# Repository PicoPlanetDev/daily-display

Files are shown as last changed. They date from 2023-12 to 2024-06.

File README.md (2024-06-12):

# daily-display

This README is a work in progress.

## Overview

Designed to be displayed on a wall-mounted screen, Daily Display combines a calendar of tasks 
for each day with a pill dispenser and reciept printer to help guide someone living with
Alzheimer's disease or dementia through their day.

Daily Display is designed to be entirely software-controlled, and all configuration can be
done remotely using a computer or smartphone.
This also allows a caretaker to check in on medication status for the patient, update their
calendar, and send messages throughout the day.

In my implementation, I mounted an old computer monitor as well as my pill dispenser mechanism
on a kitchen wall to improve conspicuousness.

## Parts List

### Electronics

- Orange Pi Zero 3 single board computer, under $35 on [Amazon](https://www.amazon.com/dp/B0CB12XS91)
  - I selected this SBC during the Raspberry Pi shortage, and it has satisfied my needs well;
  however, there are many alternatives you could try with only minor software modifications.
  - I went for the model with 1GB of RAM, but the 1.5GB is not significantly more expensive.
  Pretty much anything goes, though, and it just has to run two web servers and Chromium as a kiosk.
- PCA9685 PWM servo driver board, about $10 on [Amazon](https://www.amazon.com/s?k=pca9685)
- One servo motor (i.e. Tower Pro SG90) for each pill you'd like to dispense
  - Consider metal gears, because a jammed pill (or foreign object debris) may strip plastic gears
  - The CAD files I included are designed for four different medications, meaning four servos
- Serial thermal printer, about $50 on [Amazon](https://www.amazon.com/s?k=ttl+thermal+printer)
- TCRT5000 IR reflectance sensor, under $10 on [Amazon](https://www.amazon.com/s?k=tcrt5000)
  - Used to determine if pills have actually been dispensed, and if a hand has grabbed them from the output trays
- Computer monitor
  - I used an old 1440x900 monitor with a micro-HDMI to VGA adapter.
  - You'll pretty much always need some adapter because the Orange Pi uses micro-HDMI, but if you *had to* buy one new, I'd go for one of those 15.6" portable monitors since it would be flush with the wall (or could stand on a surface)
  - I ended up using a low profile VESA mount and some wall anchors to hang mine. It's ugly but functional.

### 3D Printed Parts

Editable source files are included in the `cad/Fusion` and `cad/STEP` directories to support the majority of CAD packages.
As the names imply, I have deleted and redacted some components of the CAD files to avoid sharing
the specific medications that I designed my system for.

You'll need to at least open these CAD files and make a few changes to match the dimensions of your
specific pills.
Included in those files is an example mechanism for a round and oval pill.
Some trial and error is necessary here, and my ziploc bag of scrapped prototype parts is overflowing.

In the `cad/3MF` directory there are ready-to-print files for the following parts:
- Thermal printer enclosure
- Pill dispenser mechanism base (holds the servo motor and customized parts)
- Sensor cover (protects the TCRT5000s from dust, bumps, and light to some degree)

If you happen to be using four pills as I am, then the following parts of the case will also work for you:
- Lower Plate
- Upper Plate
- Walls

## Source code

The backend relies on Flask, which serves JSON to a Vue frontend using Axios to make requests.

The calendar can be connected to any iCalendar-compatible service, including Google Calendar.
As of right now, the calendar integration can be customized by customizing the auto-generated
`config.ini` file in the `backend` directory with the following contents:

```
# backend/config.ini
...
calendar_url=yoururlhere
...
```

In Google Calendar, this URL can be found by hovering over the calendar name in the left navbar,
clicking the menu icon, then clicking *Settings and Sharing*, and scrolling down to the *Integrate calendar*
heading. You can then click the clipboard icon in the *Secret address in iCal format* box, and paste that URL
into the `config.ini` file.

## Installation

**Warning:** these steps are incomplete and subject to change. Proceed only with experience!

### Prerequisites

#### node via nvm

As explained in full detail at [https://github.com/nvm-sh/nvm](https://github.com/nvm-sh/nvm), run the following commands to install node using nvm.
1. Run `curl -o- https://raw.githubusercontent.com/nvm-sh/nvm/v0.39.5/install.sh | bash` to download and install nvm
2. Close and reopen your terminal
3. Ensure that `command -v nvm` returns `nvm`
4. Install the latest version of node using `nvm install node`

### Set up
1. Install all node modules required for the frontend:
```
cd whiteboard-recorder/frontend
npm install
```
2. Install the Python packages for the backend
```
cd ../backend
python3 -m venv venv
source venv/bin/activate
pip3 install -r requirements.txt
```

#### To run Daily Display on boot:
1. Copy `daily-display-backend.service` and `daily-display-frontend.service` into the `/etc/systemd/system` directory:
```bash
cd daily-display
cp daily-display-backend.service /etc/systemd/system/.
cp daily-display-frontend.service /etc/systemd/system/.
```
2. Reload the systemctl daemon:
```bash
sudo systemctl daemon-reload
```
3. Enable both services to run at boot:
```bash
sudo systemctl enable daily-display-backend.service
sudo systemctl enable daily-display-frontend.service
```
**This only enables the Daily Display software and web interface server.** To also automatically open
a fullscreen browser window, follow the below instructions.

#### To automatically start Chromium in kiosk mode:
1. Identify your operating system's application autostart feature. This tutorial will show the process for an Orange Pi Zero 3 running Debian 12 "bookworm" with the Xfce desktop environment.
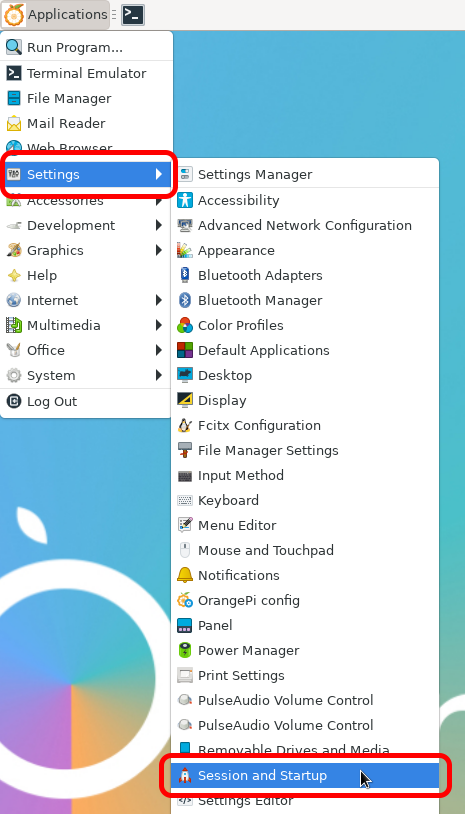
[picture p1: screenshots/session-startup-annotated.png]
Settings menu depicting the hierarchy to the Session and Startup entry


2. Launch the Application Autostart manager. For me, it was located under `Settings -> Session and Startup` on the **Application Autostart** tab.
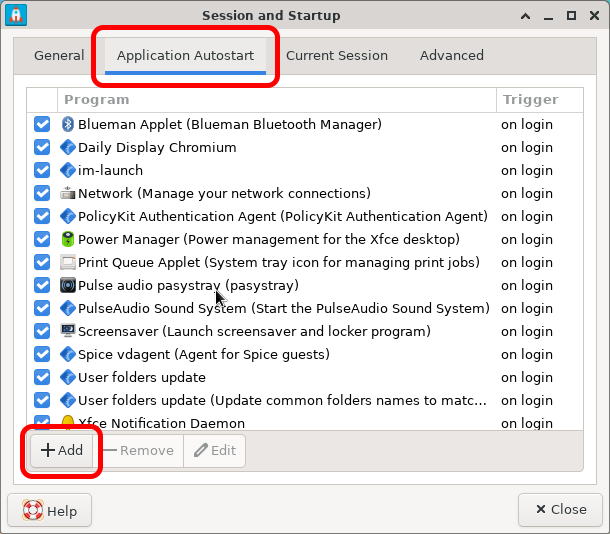
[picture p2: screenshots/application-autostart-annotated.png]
Screenshot showing the Application Autostart tab and Add button


3. Create a new entry by clicking the <kbd>+ Add</kbd> button, then fill in name and description however you like.
4. Fill the command input box with the following command:
```bash
chromium http://localhost:5173 --kiosk
```
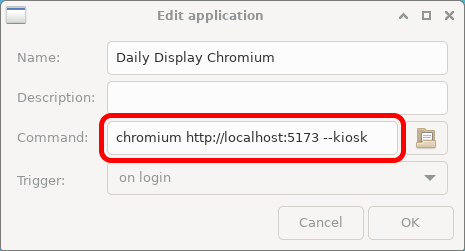
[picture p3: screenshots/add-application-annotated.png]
Screenshot showing example values for the add application box


5. Finally, click <kbd>OK</kbd> and restart the computer, ensuring that Chromium launches in fullscreen to the correct address after the computer boots up.

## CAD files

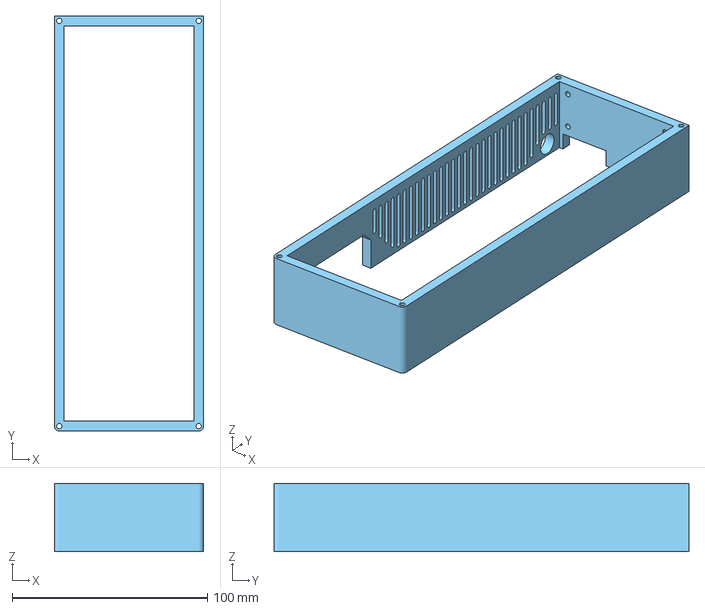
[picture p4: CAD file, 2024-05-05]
cad/3MF/Case/Walls.3mf
76.5 x 212.7 x 35.0 mm

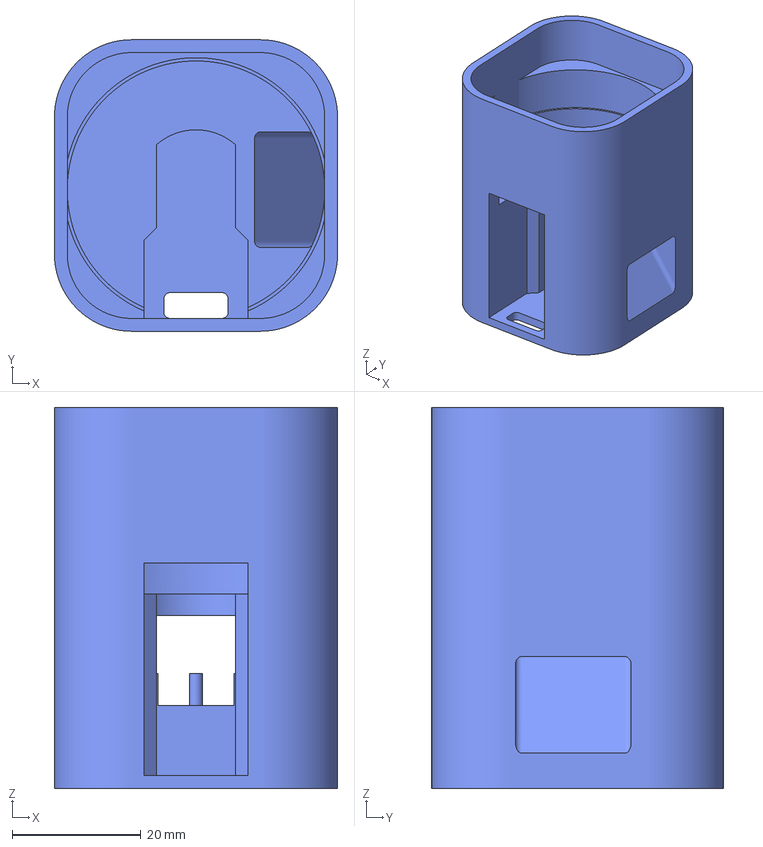
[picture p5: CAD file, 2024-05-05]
cad/3MF/Dispenser/Base.3mf
44.0 x 45.3 x 59.2 mm

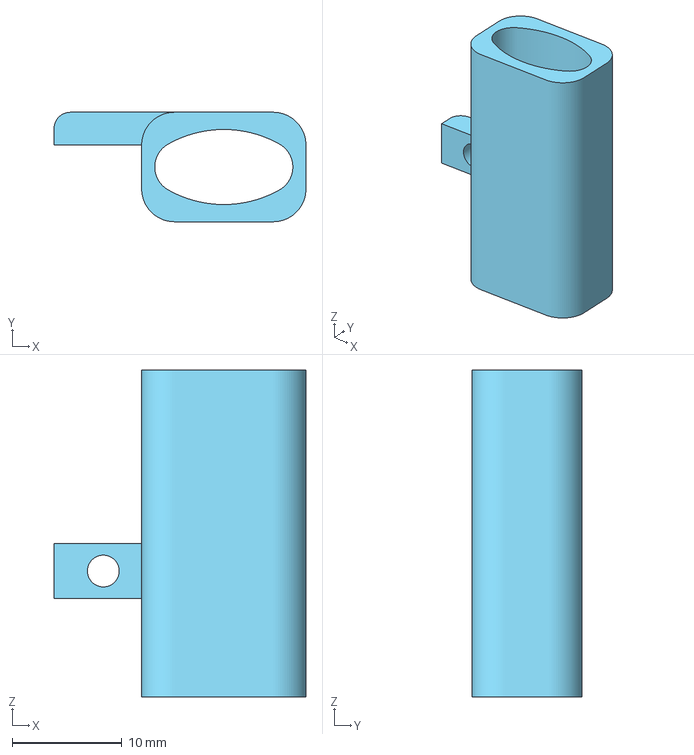
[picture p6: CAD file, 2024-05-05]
cad/3MF/Dispenser/Oval Pill Example/Oval Pill Column 1 week.3mf
23.0 x 10.0 x 29.8 mm

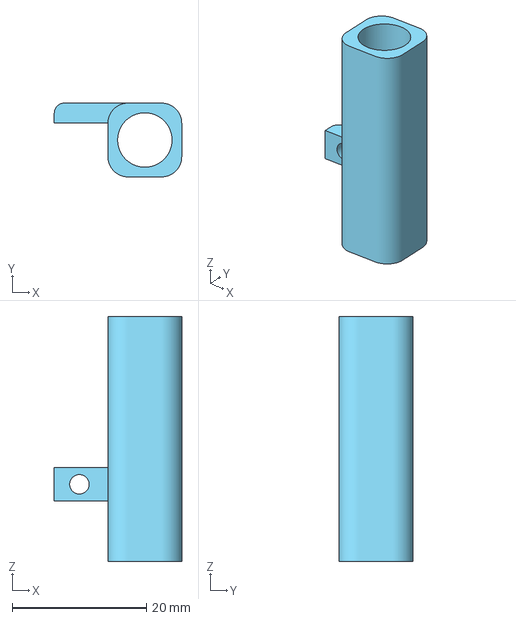
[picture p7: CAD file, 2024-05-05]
cad/3MF/Dispenser/Round Pill Example/Round Pill Column.3mf
19.0 x 11.0 x 36.5 mm

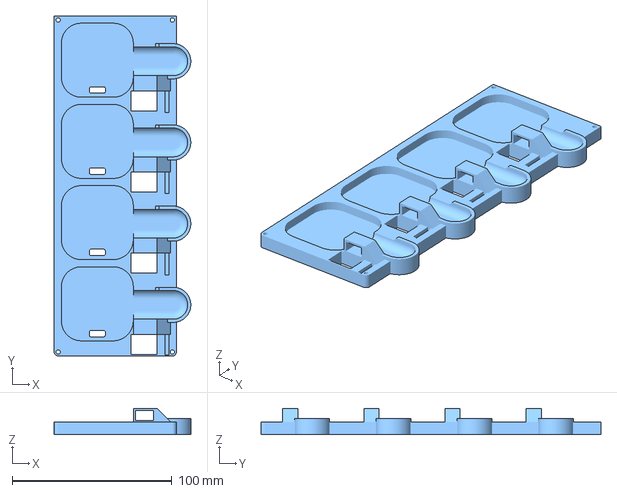
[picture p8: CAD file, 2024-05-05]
cad/3MF/Case/Upper Plate.3mf
85.5 x 212.7 x 16.5 mm

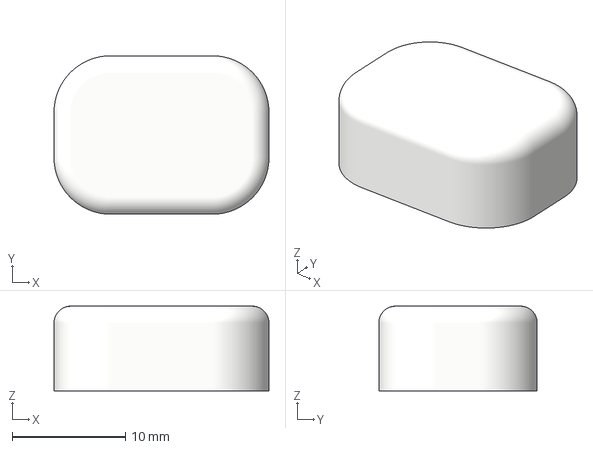
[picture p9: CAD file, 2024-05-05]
cad/3MF/Dispenser/Oval Pill Example/Oval Pill Cap.3mf
19.0 x 14.0 x 7.50 mm

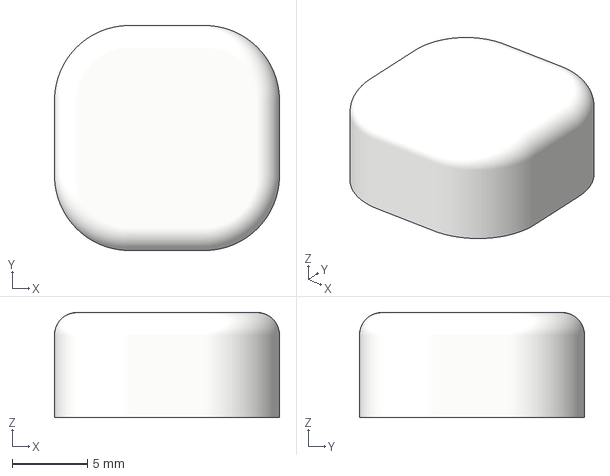
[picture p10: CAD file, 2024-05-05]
cad/3MF/Dispenser/Round Pill Example/Round Pill Cap.3mf
15.0 x 15.0 x 7.00 mm

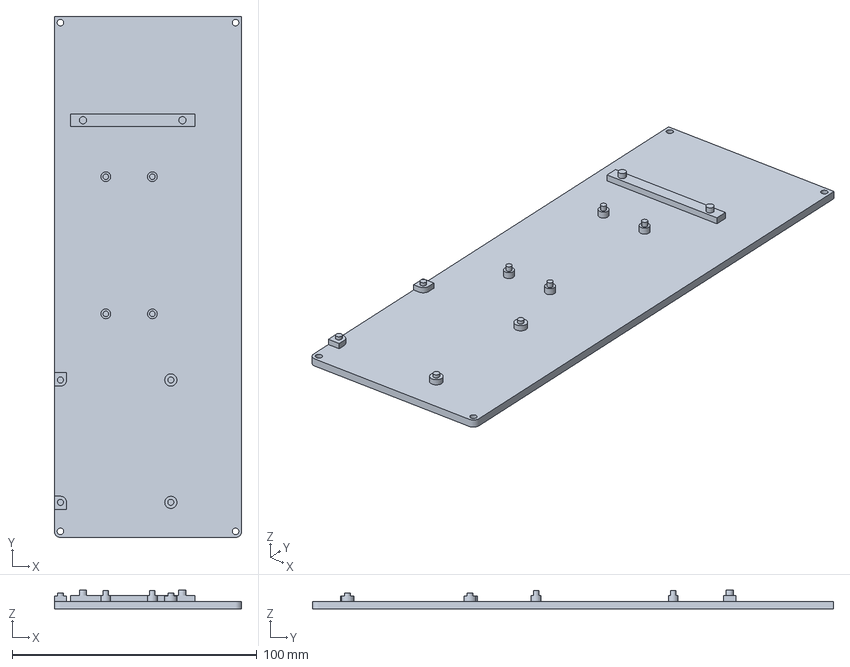
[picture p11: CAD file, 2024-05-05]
cad/3MF/Case/Lower Plate.3mf
76.5 x 212.7 x 7.60 mm

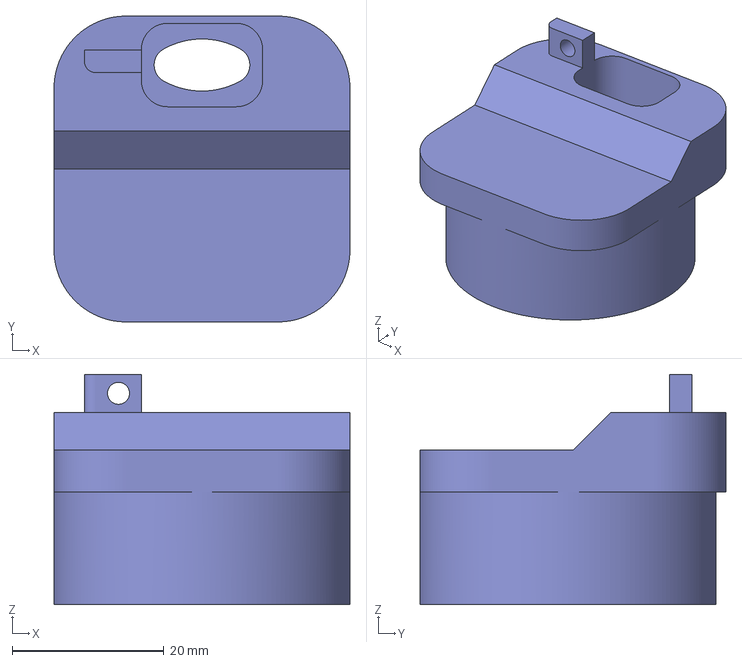
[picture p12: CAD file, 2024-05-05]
cad/3MF/Dispenser/Oval Pill Example/Oval Pill Adapter.3mf
39.0 x 40.3 x 30.3 mm

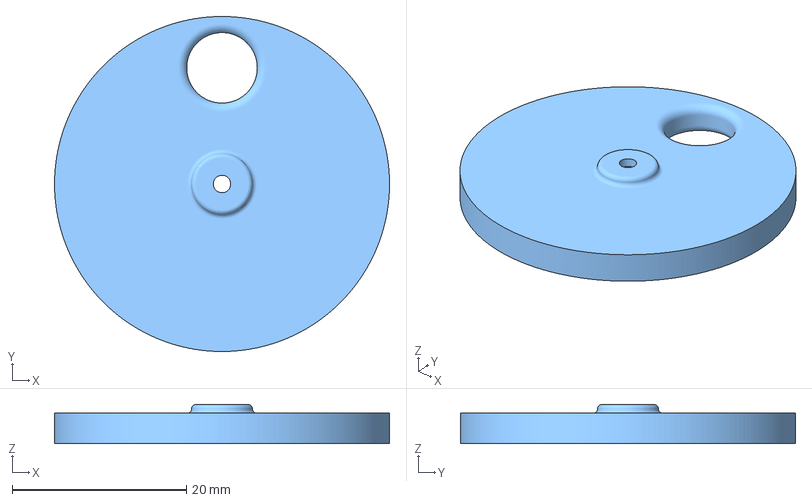
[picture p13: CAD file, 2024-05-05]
cad/3MF/Dispenser/Round Pill Example/Round Pill Spinner.3mf
38.5 x 38.5 x 4.50 mm

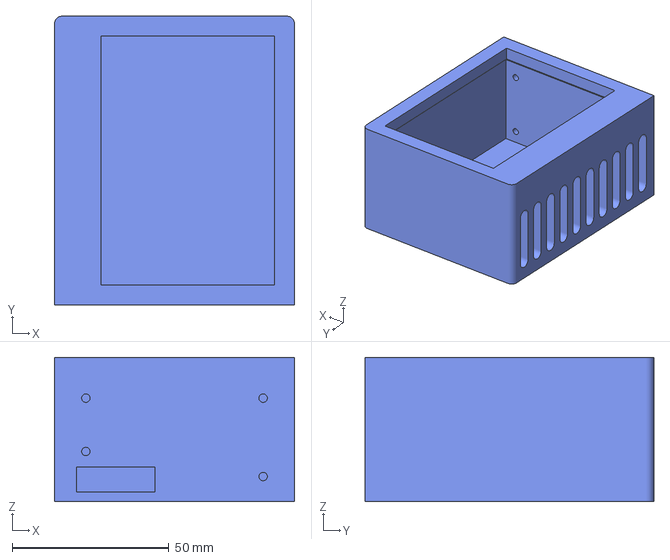
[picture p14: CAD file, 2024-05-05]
cad/3MF/Case/Printer Body.3mf
76.5 x 92.1 x 46.0 mm

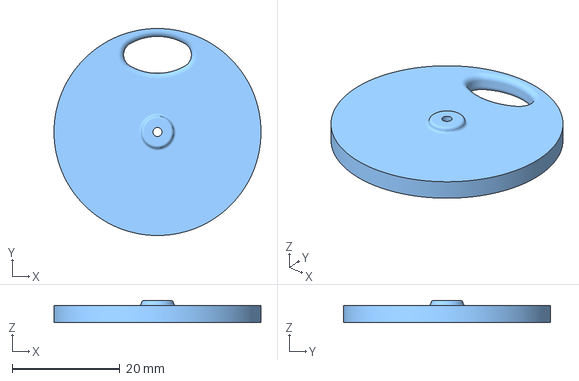
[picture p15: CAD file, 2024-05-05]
cad/3MF/Dispenser/Oval Pill Example/Oval Pill Spinner.3mf
38.5 x 38.5 x 4.10 mm

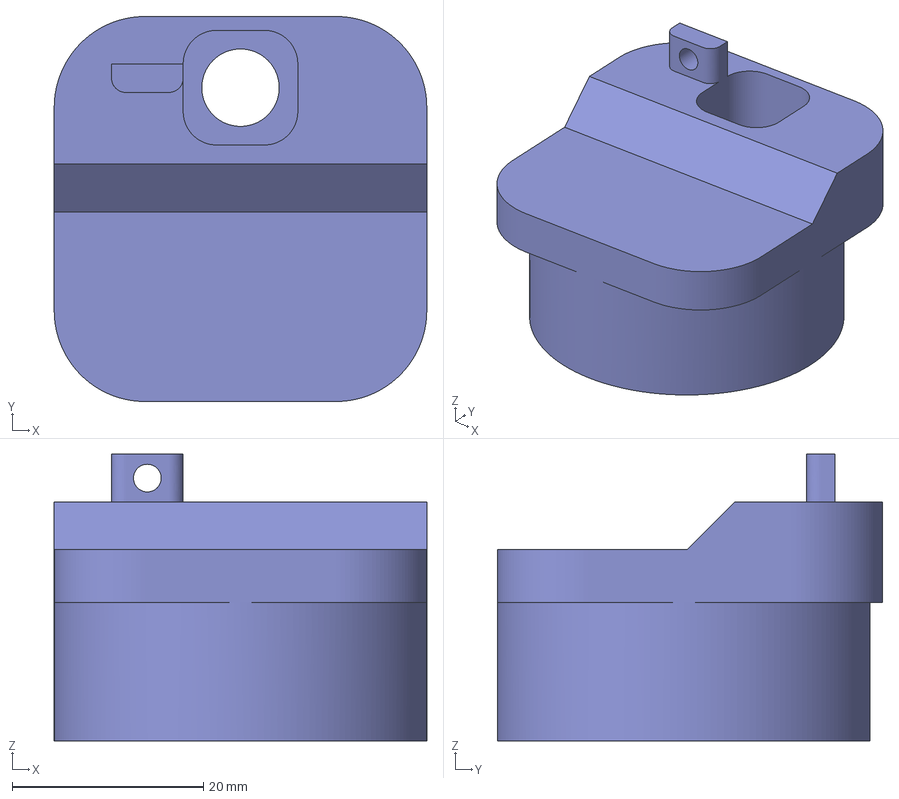
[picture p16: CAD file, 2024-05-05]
cad/3MF/Dispenser/Round Pill Example/Round Pill Adapter.3mf
39.0 x 40.3 x 30.0 mm

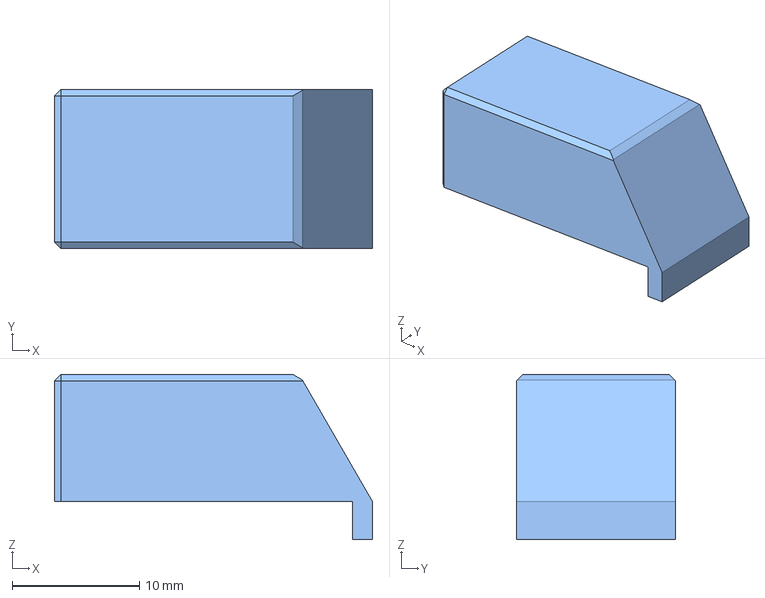
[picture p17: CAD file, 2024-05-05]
cad/3MF/Case/Sensor cover.3mf
25.0 x 12.5 x 13.0 mm

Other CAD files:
cad/3MF/Dispenser/Oval Pill Example/Oval Pill Column 2 week.3mf

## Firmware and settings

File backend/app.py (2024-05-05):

#!/venv/bin/python3
# -*- coding: utf-8 -*-
from flask import Flask, request, jsonify
from flask_cors import CORS
from calendar_helper import Calendar
from settings import Settings
from notifications import Notifications
from pills import PillDatabase
from printer import Printer
import os
import subprocess
import qrcode
import my_ip
from apscheduler.schedulers.background import BackgroundScheduler
from dispenser import Dispenser
from tzlocal import get_localzone
from datetime import datetime, timedelta

tz = get_localzone()
scheduler = BackgroundScheduler(timezone=tz)
scheduler.start()

app = Flask(__name__)
app.config.from_object(__name__)
cors = CORS(app, resources={r"/*": {"origins": "*"}})

calendar = Calendar()
settings = Settings() # config.ini is created if it doesn't exist
notifications = Notifications()
pill_database = PillDatabase()
printer = Printer()
dispenser = Dispenser(i2c_bus=3, i2c_address=0x40)

def schedule_rounds():
    for round in pill_database.get_rounds():
        round_name = round['name']
        try:
            scheduler.remove_job(round_name)
            scheduler.remove_job(f"{round_name}_unlock")
        except:
            #print("Job not found")
            pass
        
        round_time = datetime.strptime(round['time'], "%H:%M").astimezone()
        round_hour = datetime.strftime(round_time, "%H")
        round_minute = datetime.strftime(round_time, "%M")

        scheduler.add_job(handle_round, 'cron', hour=round_hour, minute=round_minute, id=round_name, args=[round_name])

        # Unlock the dispenser early
        manual_dispense_time = settings.get_config_dict()['manual_dispense']
        unlock_time = round_time - timedelta(minutes=manual_dispense_time)
        unlock_hour = datetime.strftime(unlock_time, "%H")
        unlock_minute = datetime.strftime(unlock_time, "%M")

        scheduler.add_job(unlock_dispenser, 'cron', hour=unlock_hour, minute=unlock_minute, id=f"{round_name}_unlock", args=[round_name])
        
        #print(scheduler.get_job(round_name))

def handle_round(round_name):
    print(f"Handling round {round_name}")

    # Set all pills to not be dispensed
    pill_database.set_round_not_dispensed(round_name)

    # Handle pill dispense
    pills = pill_database.get_pills()
    for pill in pills:
        if round_name in pill['round']:
            dispenser.dispense_pill(pill['dispenser'], pill['number'])
            # notifications.notification(f"{pill['name']} dispensed", title="Pill dispensed", priority="default", tags="pill")

    # Mark round as taken
    pill_database.set_round_taken_by_name(round_name, 1)

    # Handle reciept printing
    reciept_rounds = settings.get_config_dict()['receipt_rounds']
    if round_name in reciept_rounds:
        print_calendar()

def unlock_dispenser(round_name):
    pill_database.set_round_taken_by_name(round_name, 0)

schedule_rounds()

@app.route('/api/datetime', methods=['GET'])
def get_datetimes():
    response = {
        "status": "success",
        "date": calendar.get_date(),
        "time": calendar.get_time()
    }
    return jsonify(response)

@app.route('/api/events', methods=['GET'])
def get_events():
    response = {
        "status": "success",
        "events": calendar.get_events_dict(calendar.get_today(), calendar.get_today() + timedelta(days=1))
    }
    return jsonify(response)

@app.route('/api/version', methods=['GET'])
def get_version():
    response = {
        "status": "success",
        "version": "0.0.1"
    }
    return jsonify(response)

@app.route('/api/pill_warning', methods=['GET'])
def pill_warning():
    # get the next round
    next_round = pill_database.get_next_round()

    if next_round is None:
        response = {
            "status": "error",
            "message": "No rounds found"
        }
        return jsonify(response)
    
    if next_round['soon'] == True and next_round['taken'] == 0:
        response = {
        "status": "success",
        "warning": "wait",
        "pill_round": next_round['name'],
        "time_until": next_round['time_until']
        }
        return jsonify(response)
        
    if next_round['overdue'] == True and next_round['taken'] == 0:
        response = {
            "status": "success",
            "warning": "take",
            "pill_round": next_round['name'],
            "time_until": next_round['time_until']
        }
        return jsonify(response)
        
    if next_round['soon'] == False and next_round['overdue'] == False and next_round['taken'] == 0:
        response = {
            "status": "success",
            "warning": "none",
            "pill_round": next_round['name'],
            "time_until": next_round['time_until']
        }
        return jsonify(response)
    
    response = {
            "status": "error",
            "message": "No rounds found"
        }
    return jsonify(response)

@app.route('/api/settings', methods=['GET', 'POST'])
def get_settings():
    if request.method == 'GET':
        response = {
            "status": "success",
            "settings": settings.get_config_dict()
        }
        return jsonify(response)
    elif request.method == 'POST':
        data = request.get_json()
        if settings.update_config(data):
            # rerun schedule_rounds to update the schedule
            schedule_rounds()

            response = {
                "status": "success",
            }
            return jsonify(response)
        else:
            response = {
                "status": "error",
            }
            return jsonify(response)
    
    # otherwise return an http status code 405 (method not allowed)
    else:
        response = {
        "status": "error",
        "message": "Method not allowed"}
        return jsonify(response), 405

@app.route('/api/test_notification', methods=['GET'])
def test_notify():
    result = notifications.notification("Test notification from backend", title="Test notification", priority="high", tags="bell")
    if result:
        response = {
            "status": "success",
        }
        return jsonify(response)
    else:
        response = {
            "status": "error",
        }
        return jsonify(response)
    
@app.route('/api/pills', methods=['GET', 'POST', 'PUT', 'DELETE'])
def pills():
    # read
    if request.method == 'GET':
        response = {
            "status": "success",
            "pills": pill_database.get_pills()
        }
        return jsonify(response)
    
    # create
    elif request.method == 'POST':
        data = request.get_json()
        try:
            pill_database.add_pill(
                str(data['name']).strip(),
                str(data['round']).strip(),
                int(str(data['number']).strip()),
                int(str(data['dispenser']).strip())
                )
        except:
            response = {
                "status": "error",
                "message": "Invalid data"
            }
            return jsonify(response)
        else:
            notifications.notification(f"{data['name']} added", title="New pill added", priority="high", tags="pill")
            response = {
                "status": "success",
            }
            return jsonify(response)

    # update    
    elif request.method == 'PUT':
        data = request.get_json()
        try:
            pill_database.update_pill(
                int(str(data['id']).strip()),
                str(data['name']).strip(),
                str(data['round']).strip(),
                int(str(data['number']).strip()),
                int(str(data['dispenser']).strip())
                )
        except:
            response = {
                "status": "error",
                "message": "Invalid data"
            }
            return jsonify(response)
        else:
            notifications.notification(f"{data['name']} edited", title="Pill edited", priority="low", tags="pill")
            response = {
                "status": "success",
            }
            return jsonify(response)

    # delete    
    elif request.method == 'DELETE':
        data = request.get_json()
        try:
            pill_database.delete_pill(data['id'])
        except:
            response = {
                "status": "error",
                "message": "Invalid data"
            }
            return jsonify(response)
        else:
            notifications.notification(f"{data['name']} deleted", title="Pill deleted", priority="high", tags="pill")
            response = {
                "status": "success",
            }
            return jsonify(response)
        
    # otherwise return an http status code 405 (method not allowed)
    else:
        response = {
        "status": "error",
        "message": "Method not allowed"}
        return jsonify(response), 405

@app.route('/api/rounds', methods=['GET', 'POST', 'PUT', 'DELETE'])
def rounds():
    # read
    if request.method == 'GET':
        response = {
            "status": "success",
            "rounds": pill_database.get_rounds()
        }
        return jsonify(response)
    
    # create
    elif request.method == 'POST':
        data = request.get_json()
        try:
            pill_database.add_round(
                str(data['name']).strip(),
                str(data['time']).strip()
                )
        except:
            response = {
                "status": "error",
                "message": "Invalid data"
            }
            return jsonify(response)
        else:
            schedule_rounds()
            notifications.notification(f"{data['name']} added", title="New round added", priority="high", tags="clock4")
            response = {
                "status": "success",
            }
            return jsonify(response)
        
    # update
    elif request.method == 'PUT':
        data = request.get_json()
        try:
            pill_database.update_round(
                int(str(data['id']).strip()),
                    str(data['name']).strip(),
                    str(data['time']).strip()
                    )
        except:
            response = {
                "status": "error",
                "message": "Invalid data"
            }
            return jsonify(response)
        else:
            schedule_rounds()
            notifications.notification(f"{data['name']} edited", title="Round edited", priority="low", tags="clock4")
            response = {
                "status": "success",
            }
            return jsonify(response)
        
    # delete
    elif request.method == 'DELETE':
        data = request.get_json()
        try:
            pill_database.delete_round(
                int(str(data['id']).strip())
                )
        except:
            response = {
                "status": "error",
                "message": "Invalid data"
            }
            return jsonify(response)
        else:
            schedule_rounds()
            notifications.notification(f"{data['name']} deleted", title="Round deleted", priority="default", tags="clock4")
            response = {
                "status": "success",
            }
            return jsonify(response)
        
    # otherwise return an http status code 405 (method not allowed)
    else:
        response = {
        "status": "error",
        "message": "Method not allowed"}
        return jsonify(response), 405

@app.route('/api/dispensers', methods=['GET', 'POST', 'PUT', 'DELETE'])
def dispensers():
    # read
    if request.method == 'GET':
        response = {
            "status": "success",
            "dispensers": pill_database.get_dispensers()
        }
        return jsonify(response)
        
    # update
    elif request.method == 'PUT':
        data = request.get_json()
        try:
            pill_database.update_dispenser(
                int(str(data['id']).strip()),
                int(str(data['index']).strip()),
                int(str(data['servo_min']).strip()),
                int(str(data['servo_max']).strip()),
                int(str(data['angle_default']).strip()),
                int(str(data['angle_chute']).strip()),
                float(str(data['smooth_duration']).strip()),
                float(str(data['step_time']).strip()),
                int(str(data['smooth_enabled']).strip()),
                int(str(data['sensor_pin']).strip()),
                int(str(data['sensor_enabled']).strip())
                )
        except:
            response = {
                "status": "error",
                "message": "Invalid data"
            }
            return jsonify(response)
        else:
            dispenser.refresh_dispenser_data()
            notifications.notification(f"Dispenser {data['index']} edited", title="Dispenser edited", priority="default", tags="gear")
            response = {
                "status": "success",
            }
            return jsonify(response)
        
    # otherwise return an http status code 405 (method not allowed)
    else:
        response = {
        "status": "error",
        "message": "Method not allowed"}
        return jsonify(response), 405

@app.route('/api/print_receipt', methods=['GET'])
def print_receipt():
    print_calendar()
    response = {
        "status": "success",
    }
    return jsonify(response)

@app.route('/api/feed_printer', methods=['GET'])
def feed_printer():
    printer.end()
    response = {
        "status": "success",
    }
    return jsonify(response)

@app.route('/api/print_qr', methods=['GET'])
def print_qr():
    # get local ip address
    local_ip = my_ip.get_local_ip()
    link = f"http://{local_ip}:5173"
    qr = qrcode.make(link)
    printer.print_qr(qr, link, "Access on the local network")

    # attempt to get tailscale ip address
    tailscale_ip = my_ip.get_tailscale_ip()
    if tailscale_ip is not None:
        link = f"http://{tailscale_ip}:5173"
        qr = qrcode.make(link)
        printer.print_qr(qr, link, "Access with Tailscale enabled")

    response = {
        "status": "success",
    }
    return jsonify(response)

@app.route('/api/mark_round_taken', methods=['GET'])
def mark_round_taken():
    # Trying to figure out a way to mark the current round taken
    # whether that's the next manual round, or the current overdue round 
    next_round = pill_database.get_next_round()
    if next_round is not None:
        pill_database.set_round_taken_by_name(next_round['name'], 1)
        response = {
            "status": "success",
        }
        return jsonify(response)
    else:
        response = {
            "status": "error",
            "message": "No rounds found"
        }
        return jsonify(response)

@app.route('/api/cycle_dispenser', methods=['POST'])
def cycle_dispenser():
    data = request.get_json()
    try:
        dispenser.cycle_dispenser(data['index'])
        response = {
            "status": "success",
        }
    except Exception as e:
        print(e)
        response = {
            "status": "error",
        }
    return jsonify(response)

@app.route('/api/shutdown', methods=['POST'])
def shutdown():
    # determine shutdown type
    data = request.get_json()

    # execute the requested shutdown command
    if data['type'] == "poweroff":
        os.system("shutdown --poweroff now")
    elif data['type'] == "reboot":
        os.system("shutdown --reboot now")
    response = {
        "status": "success",
    }
    return jsonify(response)

@app.route('/api/update', methods=['POST'])
def update():
    # execute the update command
    os.system("./update.sh")
    response = {
        "status": "success",
    }
    return jsonify(response)

@app.route('/api/print_message', methods=['POST'])
def print_message():
    data = request.get_json()
    success = printer.print_message(data['message'], calendar.get_time())
    
    if success:
        response = {
            "status": "success",
        }
    else:
        response = {
            "status": "error",
        }
    return jsonify(response)

def print_calendar():
    date = calendar.get_date()
    calendar_events = calendar.get_events_list(calendar.get_today(), calendar.get_today() + timedelta(days=1))
    printer.print_calendar(calendar_events, date)

if __name__ == '__main__':
    notifications.notification("IP address: "+ my_ip.get_local_ip() + " (local)" + (f" | {my_ip.get_tailscale_ip()} (tailscale)" if my_ip.get_tailscale_ip() else ''), title="Daily Display turned on", priority="low", tags="rocket")
    app.run(debug=True, host='0.0.0.0')

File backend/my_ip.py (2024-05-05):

import socket
import subprocess

def get_local_ip():
    s = socket.socket(socket.AF_INET, socket.SOCK_DGRAM)
    s.settimeout(0)
    try:
        # doesn't even have to be reachable
        s.connect(('10.254.254.254', 1))
        IP = s.getsockname()[0]
    except Exception:
        IP = '127.0.0.1'
    finally:
        s.close()
    return IP

def get_tailscale_ip():
    try:
        result = subprocess.check_output(['tailscale', 'ip']).decode("utf-8") # attempt to get tailscale ip address
    except Exception as e:
        return None
    
    if "command not found" in result: return None # tailscale not installed
    else: tailscale_ip = result.split()[0] # tailscale installed, get ip address from result

    if validate_ip(tailscale_ip): return tailscale_ip # if it's a valid ip address, return it
    
    return None # invalid ip address

def validate_ip(ip_address: str):
    try:
        socket.inet_aton(ip_address) # attempt to convert to binary
        return True # it worked, valid ip
    except socket.error: # it didn't work
        return False # invalid ip

if __name__ == '__main__':
    print("IP address: "+ get_local_ip() + " (local)" + (f" | {get_tailscale_ip()} (tailscale)" if get_tailscale_ip() else ''))

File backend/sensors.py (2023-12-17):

from pills import PillDatabase
from settings import Settings
import threading

import OPi.GPIO as GPIO
import orangepi.zero3

class Sensors():
    def __init__(self):
        # Set up settings
        self.config = Settings()
        self.config_dict = self.config.get_config_dict()
        self.dispenser_enabled = self.config_dict["dispenser_enabled"]

        # Cancel if dispenser is not in use, technically not necessary because this class is only used by Dispenser
        if not self.dispenser_enabled:
            return
        
        self.pill_database = PillDatabase()
        self.refresh_dispenser_data()

        self.setup_sensors() # safe to do even if no sensors are enabled

    def refresh_dispenser_data(self):
        """Refreshes the dispenser data from the database"""
        self.dispensers = self.pill_database.get_dispensers()

    def setup_sensors(self):
        """Sets up the GPIO for the sensors"""
        self.refresh_dispenser_data()
        # Set up GPIO for the sensors
        GPIO.setmode(orangepi.zero3.BOARD)
        # Get all the pins that need to be inputs
        sensor_pins = []
        for dispenser in self.dispensers:
            if dispenser["sensor_enabled"] == 1:
                sensor_pins.append(dispenser["sensor_pin"])
        # Set them all up as inputs with pull-up resistors
        try:
            GPIO.setup(sensor_pins, GPIO.IN, pull_up_down=GPIO.PUD_UP)
        except RuntimeError as e:
            print(f"GPIO already set up, raising error: {e}")

    def register_callback(self, dispenser_index, edge, function, debounce):
        """Registers a callback for a dispenser

        Args:
            dispenser_index (int): The index of the dispenser to register the callback for
            edge (s tr): The edge to register the callback for (rising, falling, or both)
            function (function): The function to call when the callback is triggered
            debounce (int): The debounce time in milliseconds
        """
        print(f"Registering callback for dispenser {dispenser_index}")

        match edge:
            case "rising":
                trigger = GPIO.RISING
            case "falling":
                trigger = GPIO.FALLING
            case "both":
                trigger = GPIO.BOTH
            case _:
                raise ValueError("Invalid edge type")
        
        GPIO.add_event_detect(self.dispensers[dispenser_index]["sensor_pin"], trigger, callback=function, bouncetime=debounce)

    def unregister_callback(self, dispenser_index):
        """Unregisters a callback for a dispenser

        Args:
            dispenser_index (int): The index of the dispenser to unregister the callback for
        """
        print(f"Removing callback for dispenser {dispenser_index}")

        # Make a new thread to unregister the callback - this might be a bad idea
        thread = threading.Thread(target=lambda:GPIO.remove_event_detect(self.dispensers[dispenser_index]["sensor_pin"]))
        thread.start()

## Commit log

2023-08-06 Add print reciept button
2023-08-06 Added install.sh to download thermal printer library
2023-08-06 Added printer functionality
2023-08-06 Fixed issues with configparser and URLs
    [printer.py, settings.py]
2023-08-06 Added feed printer button
2023-08-06 Fixed issue with get request button
2023-08-07 Added QR code printing for link
2023-08-07 Added tailscale link to print QR
2023-08-07 Moved Adafruit_Thermal.py download into printer.py
2023-08-07 Fixed issue with multiple threads using cursor
    [pills.py]
2023-08-21 Potentially fixed timezone issue
    [app.py]
2023-08-21 Fixed application context issue
    [app.py]
2023-09-12 Finished mark taken button
2023-10-25 Changed servo actuation angles
2023-11-01 Rearranged round handling order for single power supply operation
2023-12-02 Fixed issue with disabled dispenser
    [dispenser.py]
2023-12-03 Added groundwork for dispenser sensor
2023-12-03 Removed disabled add and delete sensor code
2023-12-03 Fixed issue with not configured sensor pins (maybe)
    [app.py, dispenser.py, sensors.py]
2023-12-03 Fixed execution order issue
    [dispenser.py]
2023-12-03 See if allowing the exception fixes it
    [sensors.py]
2023-12-03 Fixed issue with wrong channel
    [sensors.py]
2023-12-03 Moved sensor callback to cycle for faster iteration
2023-12-03 Test to see if print or notifs arent working
2023-12-16 Convert pin number to dispenser index
2023-12-16 Fixed stray parenthese in printer
    [printer.py]
2023-12-17 Add print to debug remove event detect
2023-12-17 Test thread method
2023-12-17 Test more with thread
2023-12-17 Debug thread stopping
2023-12-17 Test fix for round being marked as dispensed multiple times
    [app.py, pills.py]
2023-12-17 Added Danger Zone to settings with shutdown, reboot, and update
    [app.py]
2023-12-17 Add message printing
2023-12-17 Adjust print message formatting
2023-12-17 Decrease printer end feed
2023-12-17 Clear message and scroll to top after printing or error
2023-12-17 Disable print message if printer is disabled
2024-05-05 Add CAD and 3D printing files
    [Base.3mf, Lower Plate.3mf, Oval Pill Adapter.3mf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]
